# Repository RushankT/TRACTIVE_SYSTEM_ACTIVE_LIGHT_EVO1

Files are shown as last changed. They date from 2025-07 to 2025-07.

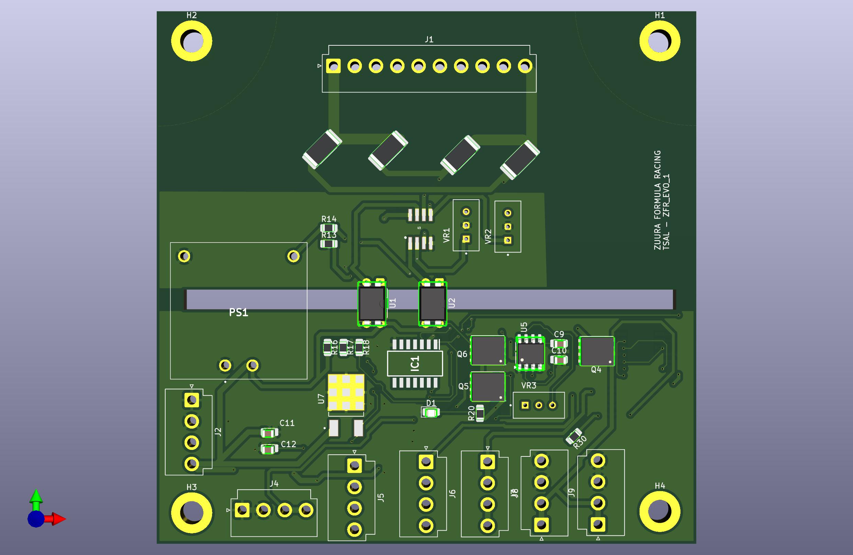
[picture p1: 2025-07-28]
TSAL_final_front.jpg

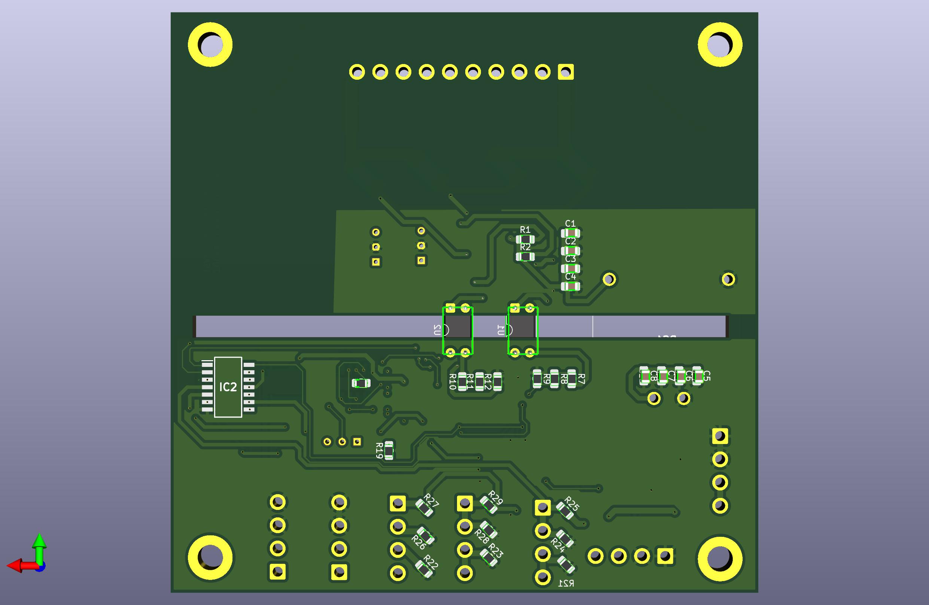
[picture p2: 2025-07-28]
TSAL_final_back.jpg

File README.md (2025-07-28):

# TRACTIVE_SYSTEM_ACTIVE_LIGHT_EVO1

## Overview

This repository contains the finalized KiCad schematic design for the **Tractive System Active Light (TSAL)** circuit, developed for our Formula Student Electric Vehicle project. The TSAL is a critical safety component used to indicate the presence of high voltage in the tractive system when the vehicle is powered on.

## Project Details

- **Project Name**: TSAL Final Design
- **Team**: Zuura Formula Racing
- **Engineer**: Rushank Talwar, EV Powertrain Lead
- **Tool Used**: KiCad (Recommended version: 6.x or newer)
- **Date**: July 2025

## Functionality

The TSAL circuit complies with Formula Student Electric rules and includes:
- A high-brightness red LED indicator visible from 3 meters.
- Blinking at ≥ 1 Hz when TS voltage > 60 VDC.
- Green Light Turns on when TS voltage < 60 VDC.
- Isolation and safety using optocouplers and fail-safe design.
- Powered by a reliable low-voltage source (e.g., 12V DC).

## File Structure

- `TSAL_final.kicad_sch`: Main schematic file for the TSAL circuit.
- (Optional) Future files: `TSAL_final.kicad_pcb`, BOM, gerber files.

## Relevant Rules

EV4.10 Tractive System Active Light

EV4.10.1 The vehicles must include a single TSAL that must indicate the TS status. The TSAL must
not perform any other functions. A TSAL with multiple LEDs in one housing is allowed.

EV4.10.2 The TSAL itself must have a red light, flashing continuously with a frequency between 2 Hz
and 5 Hz and a duty cycle of 50%, active if and only if the LVS is active and the voltage
across any DC-link capacitor exceeds
• 60VDC or 50VACRMS
• Half the nominal TS voltage
whichever is lower.

EV4.10.3 The TSAL itself must have a green light, continuously on, active if and only if the LVS is
active and ALL of the following conditions are true:
• All AIRs are opened.
• The pre-charge relay, see EV5.7.2, is opened.
• The voltage at the vehicle side of the AIRs inside the TSAC does not exceed 60VDC
or 50VACRMS.

EV4.10.4 The mentioned voltage detection must be performed inside the respective TS enclosure.

EV4.10.5 The mentioned states of the relays (opened/closed) are the actual mechanical states. The
mechanical state can differ from the intentional state, i.e. if a relay is stuck. Any circuitry
detecting the mechanical state must meet EV5.6.2.

EV4.10.6 The voltage detection circuit of the red light and the relay state and voltage detection circuit
of the green light must be independent. Any plausibility check between both lights is not
allowed. A TSAL state with both lights simultaneously active might occur and must not be
prevented.

EV4.10.7 The TSAL must:
• Be located lower than the highest point of the main hoop and including the mounting
within the rollover protection envelope, see T1.1.15.
• Be no lower than 75mm from the highest point of the main hoop.
• Not be able to contact the driver’s helmet in any circumstances.

EV4.10.8 The entire illuminated surface of the TSAL must be clearly visible:
• Except for angles less than 10° which are blocked by the main hoop.
• From a point 1:60m vertically from ground level, within 3m horizontal radius from
the TSAL.
• In direct sunlight.

EV4.10.9 The TSAL and all needed circuitry must be hard-wired electronics. Software control is not
permitted.

EV4.10.10 A green indicator light in the cockpit that is easily visible even in bright sunlight and clearly
marked with “TS off” must light up if TSAL green light is on, see EV4.10.3.

EV4.10.11 Signals influencing the TSAL and the indicator according to EV4.10.10 are SCS, see T11.9.
The individual safe state of each of the TSAL lights is off. The TSAL has an active indication
of the absence of failures (continuous green illumination) and thus the red light must not be
illuminated for a visible check, see T11.9.5.

EV4.10.12 The TSAL’s red light voltage detection circuit, see EV4.10.2, does not need to detect an
open circuit, as required by T11.9, when no voltage is present. A plausibility check must not
be implemented.

EV4.10.13 The TSAL’s green light relay state detection circuit, see EV4.10.3, does not need to detect an
open circuit, as required by T11.9, when the intentional state of the used (auxiliary) contact
is opened. A plausibility check using the intentional relay state must be implemented in a
way that the TSAL’s green light stays off after the open circuit is detectable.

EV4.10.14 The TSAL’s green light voltage detection circuit, see EV4.10.3, does not need to detect an
open circuit, as required by T11.9, when no voltage is present. A plausibility check using
the intentional relay states must be implemented in a way that the TSAL’s green light stays
off after the open circuit of the accumulator voltage detection circuit is detectable.

EV4.10.15 The latching required by EV4.10.13 and EV4.10.14 must not be triggered during normal
operation conditions and must only be reset by power cycling the LVS.

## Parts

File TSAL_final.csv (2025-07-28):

Reference | Qty | Value | DNP | Exclude from BOM | Exclude from Board | Footprint | Datasheet
C1,C5 | 2 | 100nF |  |  |  | Capacitor_SMD:C_0805_2012Metric_Pad1.18x1.45mm_HandSolder | ~
C2,C6 | 2 | 1uF |  |  |  | Capacitor_SMD:C_0805_2012Metric_Pad1.18x1.45mm_HandSolder | ~
C3,C7,C9 | 3 | 10nF |  |  |  | Capacitor_SMD:C_0805_2012Metric_Pad1.18x1.45mm_HandSolder | ~
C4,C8 | 2 | 47uF |  |  |  | Capacitor_SMD:C_0805_2012Metric_Pad1.18x1.45mm_HandSolder | ~
C10,C11,C12 | 3 | 22uF |  |  |  | Capacitor_SMD:C_0805_2012Metric_Pad1.18x1.45mm_HandSolder | ~
D1 | 1 | YELLOW LED |  |  |  | LED_SMD:LED_0805_2012Metric_Pad1.15x1.40mm_HandSolder | ~
H1,H2,H3,H4 | 4 | MountingHole_Pad |  | Excluded from BOM |  | MountingHole:MountingHole_4.3mm_M4_ISO7380_Pad_TopBottom | ~
IC1,IC2 | 2 | SN74HC08NSR |  |  |  |  | http://www.ti.com/lit/gpn/sn74hc08
J1 | 1 | Conn_01x10_Socket |  |  |  | Connector_JST:JST_VH_B10P-VH-B_1x10_P3.96mm_Vertical | ~
J2 | 1 | Conn_01x04_Socket |  |  |  | Connector_JST:JST_VH_B4P-VH-B_1x04_P3.96mm_Vertical | ~
J3 | 1 | AUX |  |  |  | Connector_JST:JST_VH_B4P-VH-B_1x04_P3.96mm_Vertical | ~
J4 | 1 | MAIN |  |  |  | Connector_JST:JST_VH_B4P-VH-B_1x04_P3.96mm_Vertical | ~
J5 | 1 | AIR+ve |  |  |  | Connector_JST:JST_VH_B4P-VH-B_1x04_P3.96mm_Vertical | ~
J6 | 1 | PRECHARGERELAY |  |  |  | Connector_JST:JST_VH_B4P-VH-B_1x04_P3.96mm_Vertical | ~
J7 | 1 | AIR-ve |  |  |  | Connector_JST:JST_VH_B4P-VH-B_1x04_P3.96mm_Vertical | ~
J8 | 1 | GREEN_LED_CONNECTOR_MAIN |  |  |  | Connector_JST:JST_VH_B4P-VH-B_1x04_P3.96mm_Vertical | ~
J9 | 1 | GREEN_LED_CONNECTOR_AUX |  |  |  | Connector_JST:JST_VH_B4P-VH-B_1x04_P3.96mm_Vertical | ~
PS1 | 1 | TMV_1212S |  |  |  | TMV_1212S:CONV_TMV_1212S
Q4,Q5,Q6 | 3 | BSC160N10NS3G |  |  |  | Package_TO_SOT_SMD:TDSON-8-1 | http://www.infineon.com/dgdl/Infineon-BSC160N10NS3-DS-v02_04-en.pdf?fileId=db3a30432239cccd01226040189a7f47
R1 | 1 | 47k Ohms |  |  |  | Resistor_SMD:R_0805_2012Metric_Pad1.20x1.40mm_HandSolder | ~
R2 | 1 | 5.1k Ohms |  |  |  | Resistor_SMD:R_0805_2012Metric_Pad1.20x1.40mm_HandSolder | ~
R3 | 1 | 240k ohms |  |  |  | Resistor_SMD:R_2512_6332Metric_Pad1.40x3.35mm_HandSolder | ~
R4,R6 | 2 | 10k ohm |  |  |  | Resistor_SMD:R_2512_6332Metric_Pad1.40x3.35mm_HandSolder | ~
R5 | 1 | 220k ohms |  |  |  | Resistor_SMD:R_2512_6332Metric_Pad1.40x3.35mm_HandSolder | ~
R7,R8,R9,R10,R11,R12,R15,R16,R17,R19,R25,R27,R29,R30 | 14 | 10k |  |  |  | Resistor_SMD:R_0805_2012Metric_Pad1.20x1.40mm_HandSolder | ~
R13,R14,R20 | 3 | 2k |  |  |  | Resistor_SMD:R_0805_2012Metric_Pad1.20x1.40mm_HandSolder | ~
R18 | 1 | 330 |  |  |  | Resistor_SMD:R_0805_2012Metric_Pad1.20x1.40mm_HandSolder | ~
R21,R22,R23 | 3 | 1 |  |  |  | Resistor_SMD:R_0805_2012Metric_Pad1.20x1.40mm_HandSolder | ~
R24,R26,R28 | 3 | 5.1k |  |  |  | Resistor_SMD:R_0805_2012Metric_Pad1.20x1.40mm_HandSolder | ~
U1,U2 | 2 | PC817 |  |  |  | Package_DIP:DIP-4_W7.62mm | http://www.soselectronic.cz/a_info/resource/d/pc817.pdf
U3 | 1 | LM393 |  |  |  | LM393 (1):SO08 | http://www.ti.com/lit/ds/symlink/lm393.pdf
U5 | 1 | NE555P |  |  |  | Package_SO:SOIC-8_3.9x4.9mm_P1.27mm | http://www.ti.com/lit/ds/symlink/ne555.pdf
U7 | 1 | L78M05CDT |  |  |  | L78M05CDT:VREG_L78M05CDT
VR1,VR3 | 2 | 3296W-1-103LF |  |  |  | 3296W-1-103LF:TRIM_3296W-1-103LF
VR2 | 1 | 3296W-1-203 |  |  |  | 3296W-1-203:TRIM_3296W-1-203

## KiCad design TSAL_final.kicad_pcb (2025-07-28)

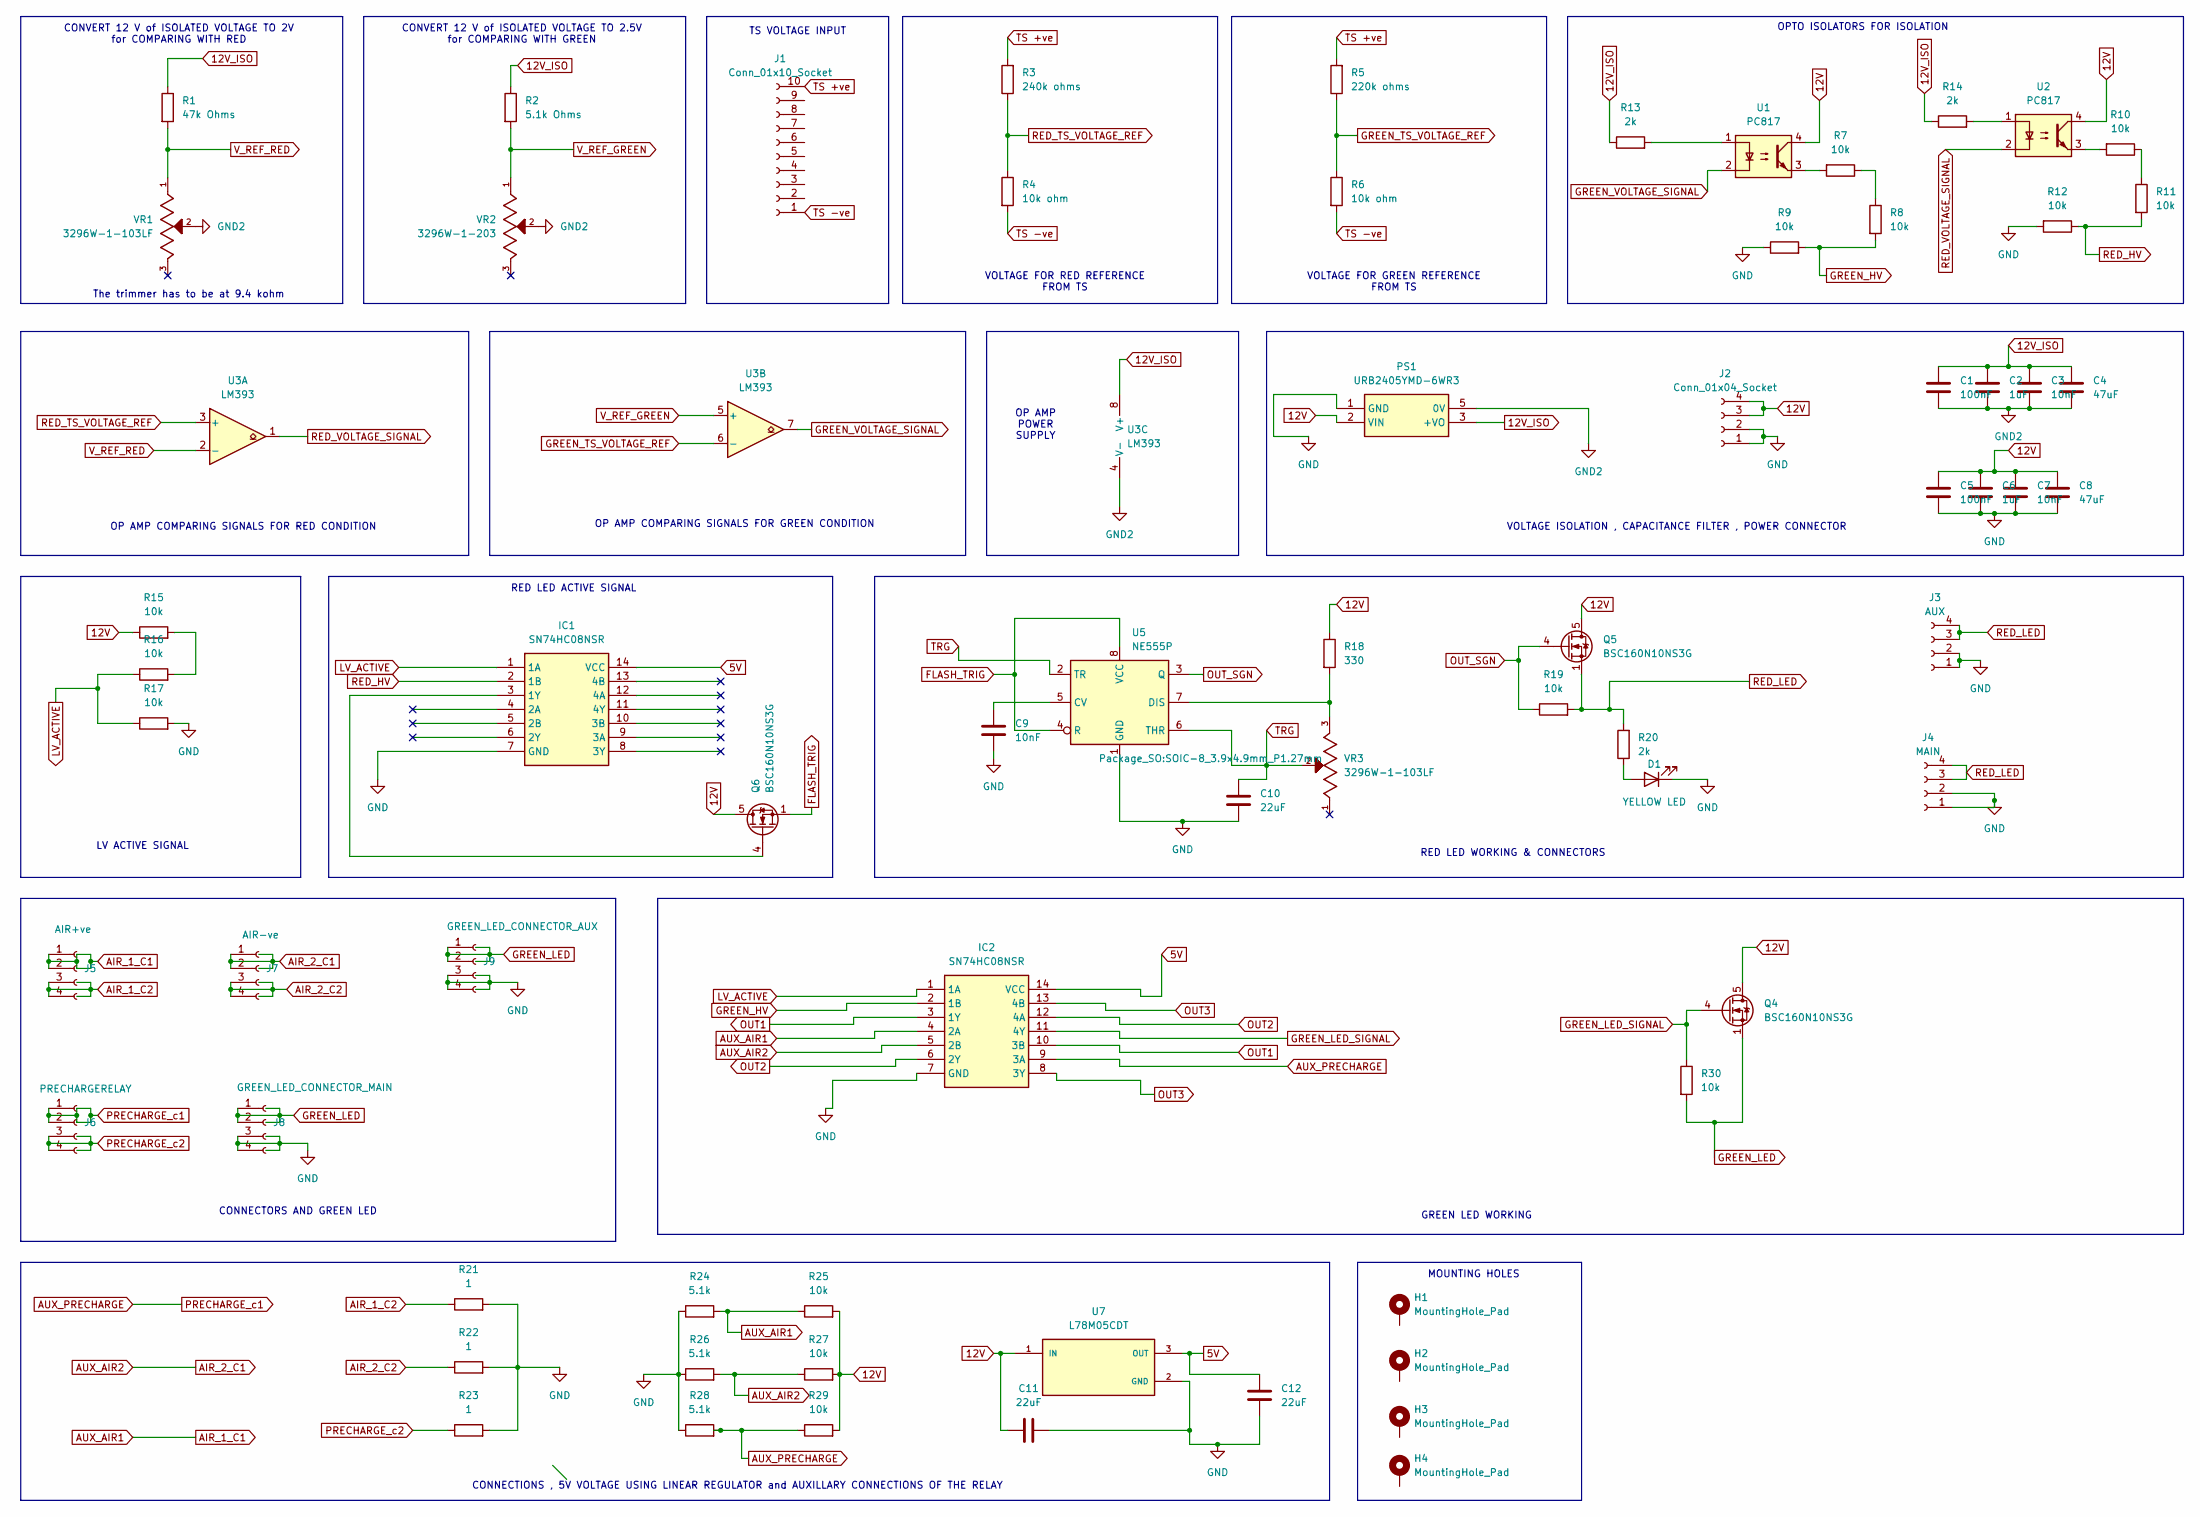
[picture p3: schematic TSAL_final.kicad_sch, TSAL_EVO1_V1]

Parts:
C1, C5: 100nF; C_0805_2012Metric_Pad1.18x1.45mm_HandSolder
C2, C6: 1uF; C_0805_2012Metric_Pad1.18x1.45mm_HandSolder
C3, C7, C9: 10nF; C_0805_2012Metric_Pad1.18x1.45mm_HandSolder
C4, C8: 47uF; C_0805_2012Metric_Pad1.18x1.45mm_HandSolder
C10, C11, C12: 22uF; C_0805_2012Metric_Pad1.18x1.45mm_HandSolder
D1: YELLOW LED; LED_0805_2012Metric_Pad1.15x1.40mm_HandSolder
H1, H2, H3, H4: MountingHole_Pad; MountingHole_4.3mm_M4_ISO7380_Pad_TopBottom
IC1, IC2: SN74HC08NSR; SOIC127P780X200-14N; Mouser Part Number 595-SN74HC08NSR
J1: Conn_01x10_Socket; JST_VH_B10P-VH-B_1x10_P3.96mm_Vertical
J2: Conn_01x04_Socket; JST_VH_B4P-VH-B_1x04_P3.96mm_Vertical
J3: AUX; JST_VH_B4P-VH-B_1x04_P3.96mm_Vertical
J4: MAIN; JST_VH_B4P-VH-B_1x04_P3.96mm_Vertical
J5: AIR+ve; JST_VH_B4P-VH-B_1x04_P3.96mm_Vertical
J6: PRECHARGERELAY; JST_VH_B4P-VH-B_1x04_P3.96mm_Vertical
J7: AIR-ve; JST_VH_B4P-VH-B_1x04_P3.96mm_Vertical
J8: GREEN_LED_CONNECTOR_MAIN; JST_VH_B4P-VH-B_1x04_P3.96mm_Vertical
J9: GREEN_LED_CONNECTOR_AUX; JST_VH_B4P-VH-B_1x04_P3.96mm_Vertical
PS1: URB2405YMD-6WR3; URB2405YMD6WR3; Manufacturer_Part_Number URB2405YMD-6WR3
Q4, Q5, Q6: BSC160N10NS3G; TDSON-8-1
R1: 47k Ohms; R_0805_2012Metric_Pad1.20x1.40mm_HandSolder
R2: 5.1k Ohms; R_0805_2012Metric_Pad1.20x1.40mm_HandSolder
R3: 240k ohms; R_2512_6332Metric_Pad1.40x3.35mm_HandSolder
R4, R6: 10k ohm; R_2512_6332Metric_Pad1.40x3.35mm_HandSolder
R5: 220k ohms; R_2512_6332Metric_Pad1.40x3.35mm_HandSolder
R7, R8, R9, R10, R11, R12, R15, R16, R17, R19, R25, R27, R29, R30: 10k; R_0805_2012Metric_Pad1.20x1.40mm_HandSolder
R13, R14, R20: 2k; R_0805_2012Metric_Pad1.20x1.40mm_HandSolder
R18: 330; R_0805_2012Metric_Pad1.20x1.40mm_HandSolder
R21, R22, R23: 1; R_0805_2012Metric_Pad1.20x1.40mm_HandSolder
R24, R26, R28: 5.1k; R_0805_2012Metric_Pad1.20x1.40mm_HandSolder
U1, U2: PC817; DIP-4_W7.62mm
U3: LM393; SO08
U5: NE555P; SOIC-8_3.9x4.9mm_P1.27mm
U7: L78M05CDT; VREG_L78M05CDT; PARTREV 24
VR1, VR3: 3296W-1-103LF; TRIM_3296W-1-103LF; PARTREV 05/16
VR2: 3296W-1-203; TRIM_3296W-1-203; PARTREV 05/16

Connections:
5V: C12.2, IC1.14 (VCC), IC2.14 (VCC), U7.3 (OUT)
12V: C5.1, C6.1, C7.1, C8.1, C11.1, J2.3, J2.4, PS1.2 (VIN), Q4.5 (D), Q5.5 (D), Q6.5 (D), R15.1, R18.1, R25.2, R27.2, R29.2, U1.4, U2.4, U7.1 (IN)
12V_ISO: C1.1, C2.1, C3.1, C4.1, PS1.3 (+VO), R1.1, R2.1, R13.1, R14.1, U3.8 (V+)
AIR_1_C1: IC2.4 (2A), J5.1, J5.2, R24.2, R25.1
AIR_1_C2: J5.3, J5.4, R21.1
AIR_2_C1: IC2.5 (2B), J7.1, J7.2, R26.2, R27.1
AIR_2_C2: J7.3, J7.4, R22.1
AUX_PRECHARGE: IC2.9 (3A), J6.1, J6.2, R28.2, R29.1
FLASH_TRIG: Q6.1 (S), Q6.2 (S), Q6.3 (S), U5.4 (R), U5.8 (VCC)
GND: C5.2, C6.2, C7.2, C8.2, C9.2, C10.2, C11.2, C12.1, D1.1 (K), IC1.7 (GND), IC2.7 (GND), J2.1, J2.2, J3.1, J3.2, J4.1, J4.2, J8.3, J8.4, J9.3, J9.4, PS1.1 (GND), R9.1, R12.2, R17.2, R21.2, R22.2, R23.2, R24.1, R26.1, R28.1, U5.1 (GND), U7.2 (GND)
GND2: C1.2, C2.2, C3.2, C4.2, PS1.5 (0V), U3.4 (V-), VR1.2, VR2.2
GREEN_HV: IC2.2 (1B), R8.2, R9.2
GREEN_LED: J8.1, J8.2, J9.1, J9.2, Q4.1 (S), Q4.2 (S), Q4.3 (S), R30.2
GREEN_LED_SIGNAL: IC2.11 (4Y), Q4.4 (G), R30.1
GREEN_TS_VOLTAGE_REF: R5.1, R6.1, U3.6 (-)
GREEN_VOLTAGE_SIGNAL: U1.2, U3.7
LV_ACTIVE: IC1.1 (1A), IC2.1 (1A), R16.1, R17.1
unnamed: D1.2 (A), R20.1
unnamed: IC1.3 (1Y), Q6.4 (G)
unnamed: R7.1, R8.1
unnamed: R7.2, U1.3
unnamed: R10.1, R11.1
unnamed: R10.2, U2.3
unnamed: R13.2, U1.1
unnamed: R14.2, U2.1
unnamed: R15.2, R16.2
unnamed: C9.1, U5.5 (CV)
unnamed: R18.2, U5.7 (DIS), VR3.3
OUT1: IC2.3 (1Y), IC2.10 (3B)
OUT2: IC2.6 (2Y), IC2.12 (4A)
OUT3: IC2.8 (3Y), IC2.13 (4B)
OUT_SGN: Q5.4 (G), R19.1, U5.3 (Q)
PRECHARGE_c2: J6.3, J6.4, R23.1
RED_HV: IC1.2 (1B), R11.2, R12.1
RED_LED: J3.3, J3.4, J4.3, J4.4, Q5.1 (S), Q5.2 (S), Q5.3 (S), R19.2, R20.2
RED_TS_VOLTAGE_REF: R3.1, R4.1, U3.3 (+)
RED_VOLTAGE_SIGNAL: U2.2, U3.1
TRG: C10.1, U5.2 (TR), U5.6 (THR), VR3.2
TS +ve: J1.10, R3.2, R5.2
TS -ve: J1.1, R4.2, R6.2
V_REF_GREEN: R2.2, U3.5 (+), VR2.1
V_REF_RED: R1.2, U3.2 (-), VR1.1

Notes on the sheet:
OPTO ISOLATORS FOR ISOLATION
VOLTAGE FOR RED REFERENCE FROM TS
TS VOLTAGE INPUT
VOLTAGE FOR GREEN REFERENCE FROM TS
OP AMP COMPARING SIGNALS FOR GREEN CONDITION
CONVERT 12 V of ISOLATED VOLTAGE TO 2V for COMPARING WITH RED
GREEN LED WORKING
CONNECTIONS , 5V VOLTAGE USING LINEAR REGULATOR and AUXILLARY CONNECTIONS OF THE RELAY
VOLTAGE ISOLATION , CAPACITANCE FILTER , POWER CONNECTOR
RED LED ACTIVE SIGNAL
LV ACTIVE SIGNAL
MOUNTING HOLES
OP AMP POWER SUPPLY
CONVERT 12 V of ISOLATED VOLTAGE TO 2.5V for COMPARING WITH GREEN
RED LED WORKING & CONNECTORS
The trimmer has to be at 9.4 kohm
OP AMP COMPARING SIGNALS FOR RED CONDITION
CONNECTORS AND GREEN LED

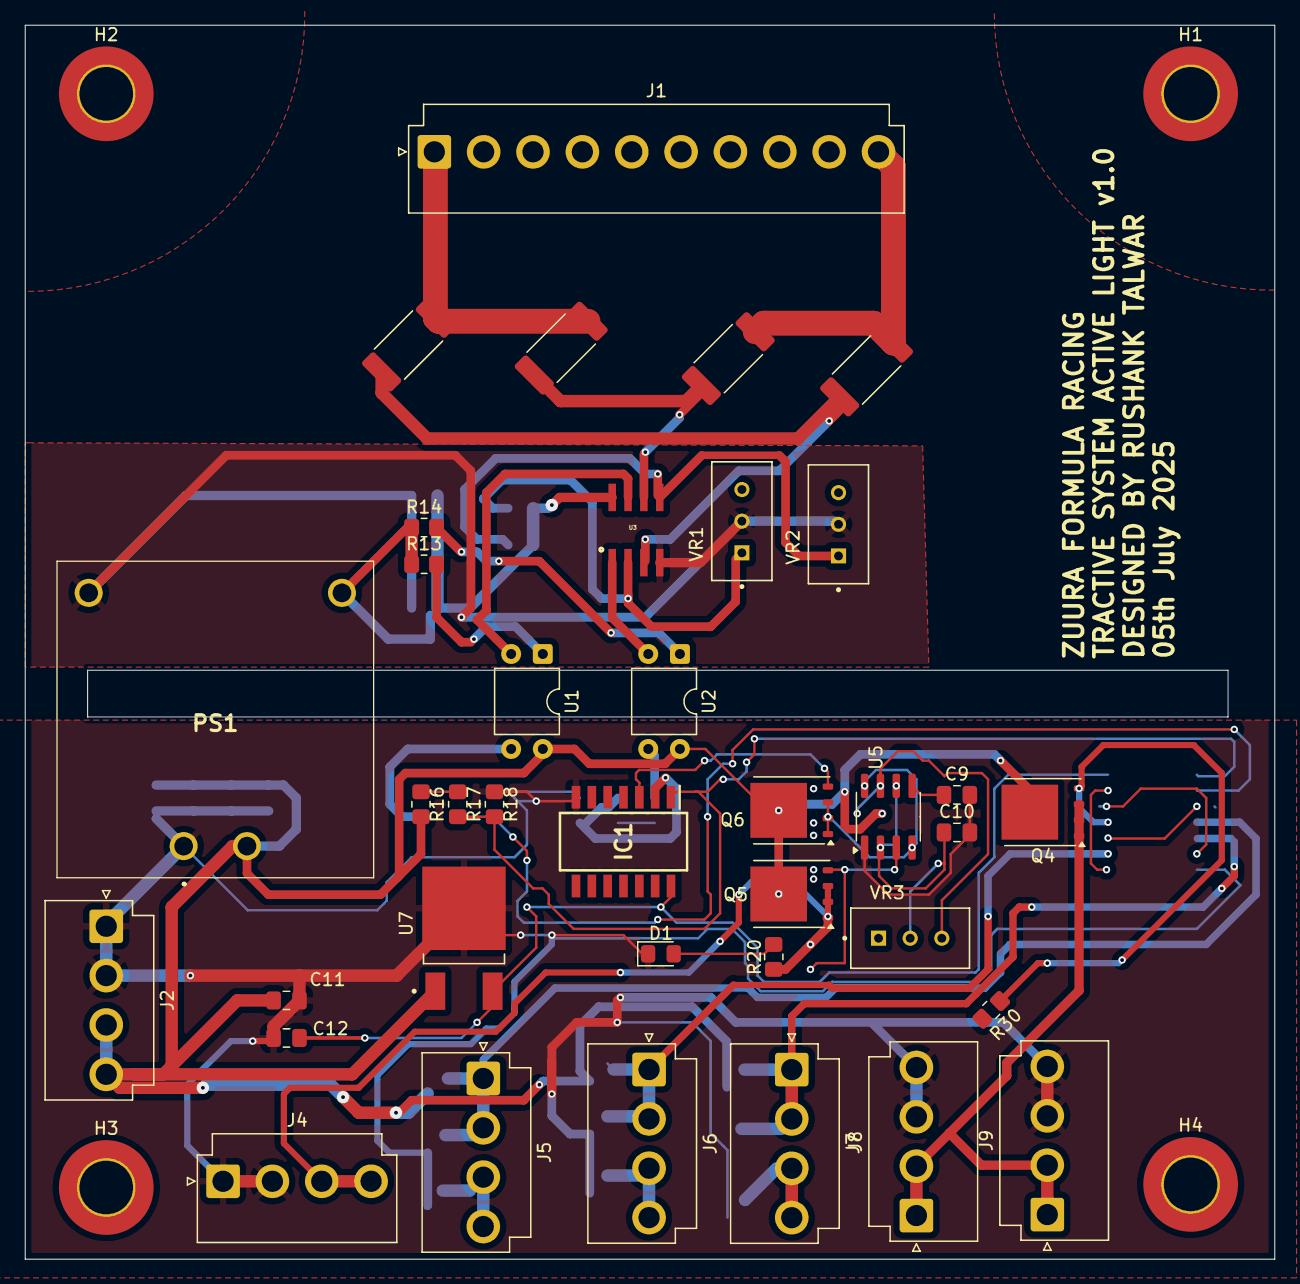
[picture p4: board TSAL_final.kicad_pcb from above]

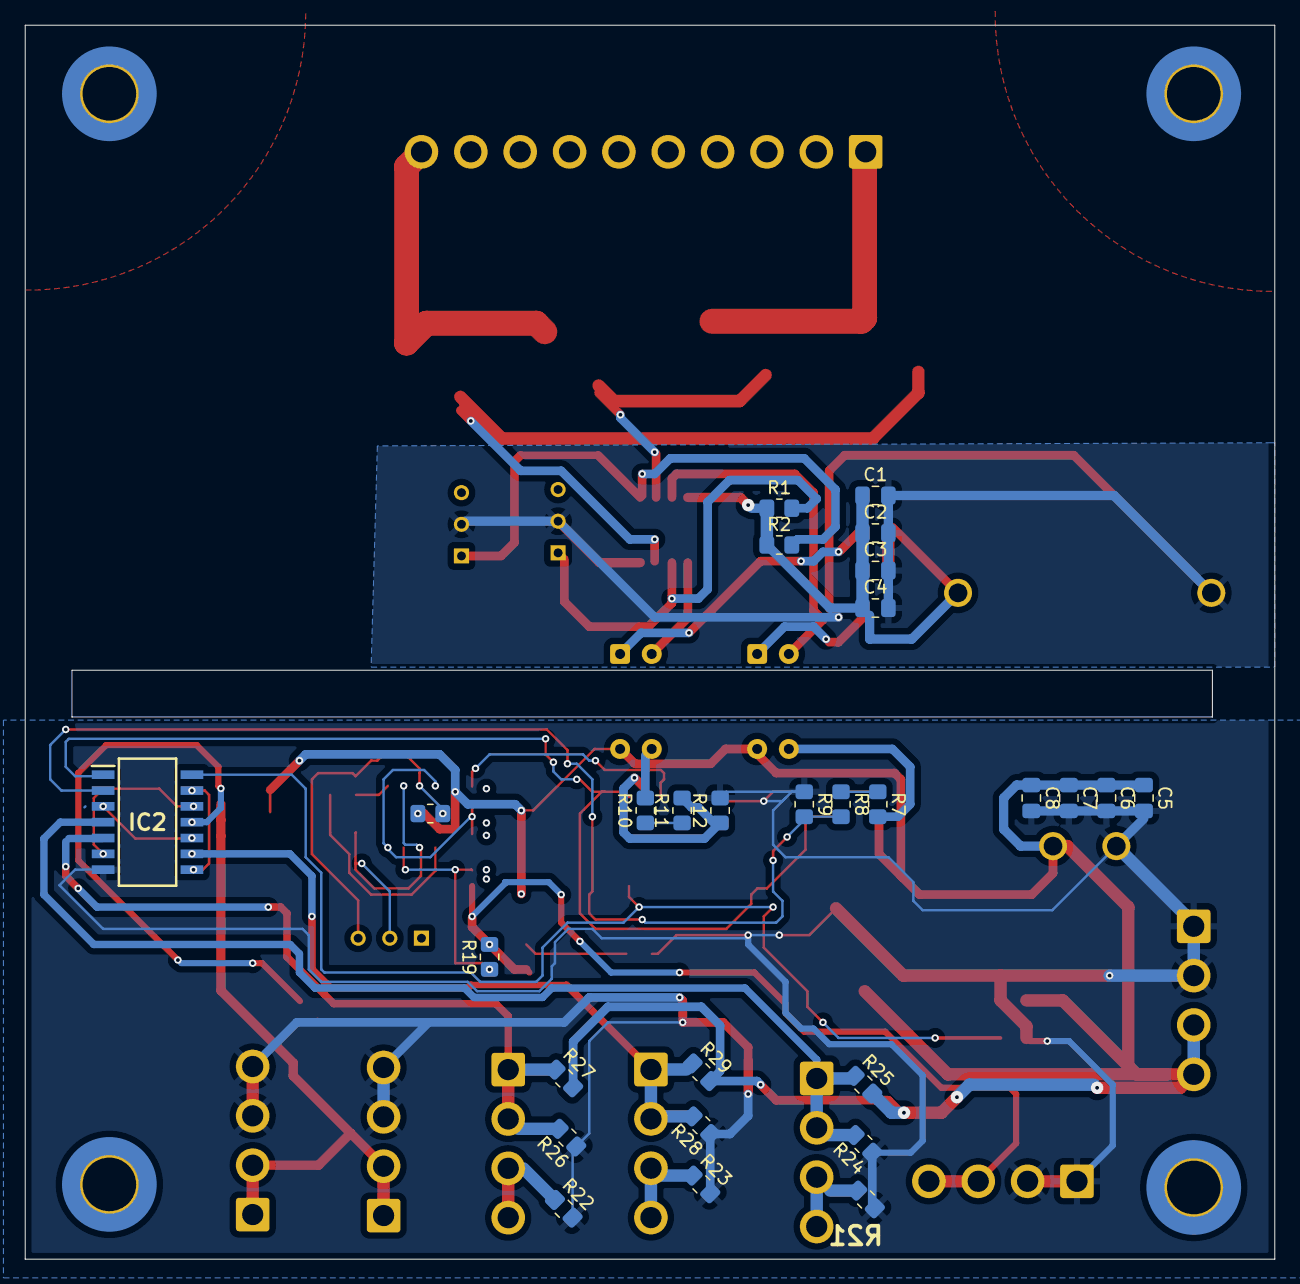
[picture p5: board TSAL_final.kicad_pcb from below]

Board: 2 copper layers, 100.2 x 99.0 mm, 69 parts (28 on the bottom side), 42 nets.
